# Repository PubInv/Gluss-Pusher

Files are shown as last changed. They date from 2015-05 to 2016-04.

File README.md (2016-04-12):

# Gluss Pusher

This is the working branch; if this is your first time here you probably want to go to our [public website](http://pubinv.github.io/Gluss-Pusher/) first.

This really needs to be changed to a new repository that talks about Gluss Robots rather than the Gluss Pusher per se.

### "The purpose of the Gluss Pusher is to enable new kinds of modular machines by making components cheap enough for hobbyist to build giant robots."

Please see [Sprint 3](https://github.com/PubInv/Gluss-Pusher/blob/master/Sprint3.md) for the latest progress.

Attempt to create simple, cheap linear actuator for giant robots and other tasks

This Repo is to hold research related to the invention of a new kind of linear actuator.

As part of the PIFAH project, this is completely open-source (both hardware and software) and everything be released either
under Creative Commons Share Alike, or the GPL.

As explained in the PIFAH/PIFAH repository, we welcome your contributions and participations.  Contact me to see how to
participate.

## Motivation

I would like to build robots based on large numbers of very simple components that can lengthen or shorten themselves.  Buckminster Fuller invented the Octet truss, a beautiful space-filling structure of alternating tetrahedra and octohedra. Or perhaps it would be more accurate to say that the universe invented and Bucky promoted it.

If we imagine a "truss" that acts like a "glass" we get a "gluss" that can move like a "slug".  That is, I want a system that can ooze about like a slug.

Linear actuators are standard components that can be purchased off-the-shelf.  However, they are rather expesnsive, at about $100 a piece. They are also more forceful and more precise that what we need to build an experimental "gluss".  Although it would be wonderful to spend $10K to build a power 100-element gluss, I think it makes more sense to attempt to use simpler components.

I also believe there is value in general for linear actuators in a cheaper, weaker part of the design spectrum.  Such actuators might be called "mechanisms" rather than "machines" in technical parlance. A machine deals with forces, a mechanism is concerned only with positioning.

# Related Links

http://en.wikipedia.org/wiki/Halbach_array

I don't understand why there isn't a good online simulator---perhaps I should write one.  This looks like it might work:

http://www.mare.ee/indrek/ephi/

http://en.wikipedia.org/wiki/Tubular_linear_motor

http://eprints.whiterose.ac.uk/852/1/wangjb15.pdf

I'm afraid I don't know enough about magnetism to really follow the equestions.  The purpose of this paper is to provide a model for linear permanent magnet machines.  I think it would be very valuable if you trying to optimize a design, or understand the force/current/voltage relationship. It is hard for me to understand exactly how to use this research.

This firm seems to make great ones, but doesn't list prices, so one can assume they are expensive:

http://www.linmot.com/fileadmin//user_upload/Downloads/databooks/0185-1100-E_1V0_Product_Overview.pdf

Here is a nice description:

http://machinedesign.com/news/linear-actuators-get-servo-look

So the terms "linear motor", "direct drive actuator", "tubular permantne magnet motor" are all used in this area.  The central rod should probably be called the "thrust rod".

This PhD Thesis looks excellent by Bryan P. Ruddy looks excellent:

http://hdl.handle.net/1721.1/78177

Reading Ruddy's dissertaton, it seems like the real contribution that I can make here is to move this out of the laboratory and into the realm of practice.  If we can make this kind of work available to hobbyist and the maker moverment, it seems that we could make very rapid progress on a really fundamental technology.

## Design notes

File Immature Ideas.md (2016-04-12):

# Idea: Use a Ferrofluid to create a simple actuator

I recenctly purchased and played around a bit with a ferrofluid. Because it is attracted to a magnetism, it seems
likely that if we put ferrofluid in a cylindrical bladder, we could apply a field to draw the fluid into a lump
(perhaps in the middle) thereby shortenining the cylinder.

# Idea: Can we use a simple air-gap filling apporach

I now wonder if we could modify the geometry of a solenoid to make a "long-throw" solenoid.  I believe the
basic prinicple that iron will be pulled in to fill an magnetized air gap could be used.

In this approach, we produce relative long magnets and use a relatively long iron core.  I don't know 
how much force is exerted in this "long model", but if enough is exerted, this could be a very elegant solution.
I think I can test this very quickly with the equipment that I have, though it will be hard to 
quantify---I need to get scientific and skilled at quanitfying these forces.

* * *

After a simple test, this seems not to be very useful.  the force for a piece of iron to be equalized between the two poles of a magnet seems either nonexistent or so low as to not be useful.  I suppose that my intuition was simply wrong about this.

# Idea: Using symmetric coils as both sensing and forced drivers.

It seems to me that if I have a set of symmetric coils arranged on the magnetic comb at something other than the comb periodicity, it should be able to detect where we are without additional sensors by applying slight currents to one comb while listening to voltage change in the other combs.  It would be very elegant in this way if we could determine our physical state.  This is simpler if you imagine a toroidal comb, rather than a linear comb, but the point is perhaps the same.

If you know where you are, you know which coil(s) to drive and which direction to drive them.  As an experiment, we could see if we can listen with an Arduino for slight motion --- even sonic frequency vibrations!

This is very elegant, because you are using more "smarts" --- putting more intelligence into the microcrontroller, without the need for hall-effect sensors (which could be used as well.)

The whole system is also thus becoming more "alive" --- it could tell when it is pushed.  It could even be pushed again something and perhaps determine how yielding it is. It is also inexpensive. Such a system could avoid the need for locking with a solenoid, by replacing it with active locking and active resistance.  This could be an extraordinarily elegant system.

# Idea: Universal rotation system

It would be really lovely if we got the above system working and then builded a true 3-degree of rotational freedom joint using the principle of geodesic dome construction to produce radail "combs" that could interact in the same way.  Imagine an omni-triangulated robot that had true 3-DOF manipulators!  All basically built with nothing but magnets and coils.  The geometric design freedom would be tremendous.

# Idea: (For Demonstration) An winged man costume...

This is sort of a cosplay idea.  Build a chest harness that has a back or chest keel.  Attach wings.  Have the linear actuator drive the wings based on buttons actuated by the hands (or in a harness.)

# Idea: Using Ferrofluid in a tube to extend the reach of the linear motor...

A fundamental problem with my current desigs is that you can only have so many magnets in contact with some many coils.  The higher the number in proximity, the more efficiency you have, but the lower stroke length.  The higher the stroke length, the more magnets or coils are wasted.  This could be changed by some complicated repositioning, but it would seem only at the expense of great complication to the moving parts.

However, what if ferrofluid confined to a tube would allow us to to make a magent of essentially changing length?  Then we could magnetize the thing with a single coil in a static position, but move the end (and the point of greatest flux change) to any position within the tube.

# Idea: use the comb and rotational magnets to produce latches....

Probably these need to latch in both directions to get the wedge effect, but that should be entirely possible.  I believe that by placing extra magnets in the carrier (not the push rod) and simply having them rotate out of the way in the presence of an applied B-field (which is easy to achieve), we should be able to make a physically strong latching system, at the cost of some increased weight in the carrier.  This would make a capactitor based "pump-and-rest" system more reasonable, and avoid us enterring a heavy duty cycle.

# Idea: using a twisting motion of the pushrod to lock it in place.

The Gluss Pusher currently doesn't have a way to lock the pushrod in place.  One way would be to have tabs added to the push rod, and grooves in the channel with slots.  By rotating the pushrod, you would free it for vertical motion, and by rotating it back you would lock it in place.  The rotation could be done with magnets in the push rod, or even rollers.  I think this would make it a lot less elegant however.

## Idea: Robotic Massage

One of the things that could be done with a 3-Gluss-member system is to make a massage robot.  The idea would be perhaps to put a ball or wheel at the end to a tetrahedron and have it pummel and roll the client. No doubt it would require a bit more sensing to be comfortable and a control mechanism, but in principle it should be possible with my system at low cost.

## Idea: Fire-Hose Robot

A Gluss could potentially climb into the window of a burning building, carrrying a fire hose.  (This idea came from a conversation with Jacqueline Kazil.) This could be controlled by a firefighter on the ground controlling a model. This would potentially allow water or a flame-retardant to be delivered more precisely to the source of fire.

## Idea: Tent Setup

This idea also came from a conversation with Jackie Kazil.  Imagine a gluss used to automatically setup a tent frame very quickly.

## Idea: (Important)

I believe we could construct an augmented octahedron. That is, make an octahedron, and add 4 tetahedron that will act as legs or pseudopods. The point that aims upward can shift to shift weight so that one of the legs may be lifted. I suspect in this way we could build an effective, and relatively inexpensive, walking robot, that would remain would have the advantages of gluss.  That is, it would be capable of other configurations as well, while remaining completely polymorphic.  Note: Possibly this would require a different a rotor, which would not be too hard---not sure about that, I have to check the math. 

This would require 1 octahedron (12 glussions), plus 4 legs, each requires 3 additional glussions --- so a total of 24 glussions.  At current prices this would cost one about $2400, which seems rather expensive.

Note that this geometry the center point would touch the ground in the most relaxed position --- although if they maintained some eccentricity, this might not be a problem, it is possible that better designs exist. For example, we could easily adjust the platform---but then we would be deviated from our basic principle of using only standard glussions.  Perhaps it is best just to use standard glussions and accept the eccentricity.  I don't particularly relish spending $2500 to test this idea --- but note that the resulting robot would be much larger and possibly capable of carrying much more than most robots.

## Idea: Maybe we can make really cheap by making a linear induction motor....

Last night I did the math and it requires 13 octet pairs to build a mast capable of forming a circle with a Q of 1.5. That works out to 108 glussions. At $70 a piece, that's a lot of change. My permanent magnet based system can potentionally lower that price, but only so much.  If we could use a linear induction motor instead, we could start to get really cheap---possibly $15 per glussion.  Of course, the controller will still be needed, and such a system won't hold its position without additional hardware or constant power---but still, a 5-fold cost reduction is worth exploring.  After all, the screw-type actuators also collapse under a sufficently high backdrive force (31 Newtons, in the case of the Firgelli model I am using.)

<br /><span xmlns:dct="http://purl.org/dc/terms/" href="http://purl.org/dc/dcmitype/Text" property="dct:title" rel="dct:type">PIFAH: Immature Ideas</span> by <a xmlns:cc="http://creativecommons.org/ns#" href="https://github.com/PubInv/PIFAH" property="cc:attributionName" rel="cc:attributionURL">Robert L. Read</a> is licensed under a <a rel="license" href="http://creativecommons.org/licenses/by-sa/4.0/">Creative Commons Attribution-ShareAlike 4.0 International License</a>.<br />Based on a work at <a xmlns:dct="http://purl.org/dc/terms/" href="https://github.com/PubInv/PIFAH" rel="dct:source">https://github.com/PubInv/PIFAH</a>.

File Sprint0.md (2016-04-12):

Note: This was actually Sprint4 or PIFAH, before I decided to make this its own project.

## Stories

* Figure out if I can get the 1/4" x 1/2" magnets into a tube for making the actuator.
* Experiment with apply the current loop to these magnets---I believe we will get a strong push from them.
* Try to construct an initial prototype of the actuator using just a power supply.
* Construct a new MOSFET circuit (similar to old one) and see if I can drive it fro the Arduino to properly
move the actuator to a different state.
* See if I can order an H-Bridge that will allow me to reverse current flow in a way that will allow us to change
the actuator state in both directions.

As a matter of procedure, if I can get anything working I will create a new Repo for this project.

## Log

In the last two days, since Mini Make Faire, I worked on the actuator.

I build a coil and a set of magnets, placed in some foamcore.  I was able to get it to move.

I think worked much harder, and built a good plywood holder for 6 of the 1/4 x 1/2 magnets. I held these in place in polycarbonate taped together.

I tried it, and it didn't work.  That is, it twitched. It did not do what I need it to do: move to one of the "pole" positions based on the current.

I was quite surprised that the force was insufficient, although my coil has only 30 or 40 turns, and mow power supply cuts off at 5 amps. Nonetheless, it was a failure.

I am attempting to construct the magnetic actuator anew with a poster-board wrapper. Hopefully this will be both "slicker", having less friction, and will be lighter. It is possible this model will work.  It is possible that I will have to go back to the drawing boards.

imag0170

imag0161
imag0163
imag0165
imag0167
imag0169

## Wednesday

I learned that the tightness of the windings really matters.  I'm now getting a few ounces of force, I imagine.  I have a strange assymetry in the actuator I built that I can't explain.

I tried using an aluminum tube and it seemed very weak --- possibly the Krebbs effect at work.

I embedded two magnets in a wooden dowel.  When that is placed inside a PVC pipe with a coil around it, I am starting to see the kind of behavior I expect, though the weird assymetry persists.

I am very tempted to buy some better materials---I know that will make a difference, but it is also a delay and an expense.  I want to carry on with as many experiments as I can at present.

General lesson:  It is really hard to get a coil 3/4" wide to discrimnate a magnet only a 1/2" long.

I've got a bistable system, but it should have 3 or 4 poles (for 2 or 3 magnets), that is, 3 stable conditions.  In stead it seems to "wash out" in the middle.  it is as if the flux within the coil is swamped by the flux at either end.

## Wednesday Night

I am a fool, but I have done it! My expectations were wrong.  It is clear if now that if you build a "comb" with alternative North and South poles each one will represent a stable position (probably just on the opposite side of the charged coil.)  I can now, just by switching power, move randomly through 4 stable states with 5 magnets.
The motion is random now because I can't control which state it will move to when I switch current direction driving it out of the current state.  However, that can be fixed easily in the future.

I think this is a great success.  IF this can be tied into a frame that provides permanent magnet latching, and IF I can get an Arduino to successfully switch on and reverse power (such as with the MOSFET circuit I built earlier, then it seems that I might have actually created something useful: A cheap, long-through, multi-polar linear actuator.

Note: I messed up the spacing on the magnets in my actuator.  I may have to redo in order to get the latching to work properly. Ideally I would have better materials by that time.

## Friday Night

The two-dimensional attempt basically didn't move very well.

I switched back to a tubular approach, basically re-inventing the tubular linear motor.

This actually "worked" in that I could easily drive a 2" crest-to-crest change using the coil.  This is similar to a 
coil gun, with a permanent magnet in place.

imag0171

imag0172

imag0173

I have learned a lot this sprint, though perhaps that is only a sign of how ignorant I am.

Let me try to summarize:

* Magnetic field computations are actually quite difficult. Unlike electrostatic compuations, the "field" the field is modified by anything ferrous. It is in fact quite difficult to to analytically figure out the forces. Also, there is no good free online simulation!
* I believe it IS possible to build a repulsive system, but it is rather complicated. Naive approaches produce a "pinching" of attractive approaches.
* The tightness of the coil is really quite important.  A lot of flux is wasted if the coil is larger than necessary.
* My system provides no control --- I can change state but can't control direction. It is fairly obvious how to control it with a separate additional coils.
* The best way to really handle this is to have a microcontroller really understand the position of the shuttle. I don't know a good way to do this.
* This is obvious, but if you take iron it will move to a central position on the coil.
* Using my 8-volt system with a limited amperage, I can make a nail repulse a small magnet.  However, my home-made electronmagnes are in general not as powerful as the neodymium magnets.
* I CAN easily build a latching system with the permanent magnets.  It is interesting to imagine a latching system that cooperates with the electromagnetic motion.  However, I now believe this is a distraction---getting the driving working is hard enough, and we can latch with a solenoid mechanically to be stronger and cheaper (I think) than we can ever hope to be with this pure magnets.

I have created a new repo: https://github.com/PubInv/Linear-Actuator and will probably move much of this file to that repo.

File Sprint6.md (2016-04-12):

Sprint 5 saw the successful completions of the [CoilChoice tool](http://pubinv.github.io/CoilChoice/).
It was a strenuous effort and I am quite proud of it, though as far as I can tell nobody has noticed it yet.

# Theme

I believe the main theme of this sprint is to return to more 3D design.

I have what I believe is an idea for limited ball-and-socket joints for the Octet joints that is worthy of the title
"invention".  It is worth about 1 micro-Fuller, I think.  

In addition to that, I need to redesign the stator, and produce a stator-tube end cap to hold the position sensing electronis.
Basically we are now moving toward a completely scalable and independent "Glussion".

### Measurement of force of existing system.

At 12 volts, turning scale sideways, the highest force I can measure in a holding pattern 98 grams. 
At 18 volts, it is 160 grams. At 24V, 235 grams. At 30 Volts it began smoking very quickly! This heat definitely softened, perhaps destructively, the PLA plastic.

I expected this to be low, but this is really bad---I estimate we need about 10 times this much force to have a viable system.

I believe I am using 32 gauge wire right now. CoilChoice suggests that I should use 30 gauge wire.  However, it still seems somewhat unlike that we can get up to a 22 newton (1 kilogram of force system) with a 2-amp limitation.  It seems absolutely essential that we go up to 5 amps.

Our current coils provably have about 250 ampere turns at 12 volts. A 5 amp system using 28 gauge wire should provide about 750 ampere turns -- about 3 newtons, which still sucks.  

It seems possible that I should perhaps abandon this approach, or at least get the Phidget's actuators for comparison.

Quite possibly this whole project is bogus because of the difficulty of producing force in this way.

I think is pretty important now that I test the lithium io battery approach.

Using this battery:

https://www.fasttech.com/product/1895004-dc-1298a-12-6v-9800mah-rechargeable-li-ion

I was able to get 148 grams of holding power.

# Formulation of a multi-glussion connector problem

Assuming that we use a symmertic circular section of a sphere as the center of our disc, what is the greatest possible ration of L to S, where L is the longest distance and S is the shortest of our glussion, that you can connect with a tetrahedronal (or planar) connector?

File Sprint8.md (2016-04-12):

# Sprint 8 - Saturday October 3rd

Very thrilled with with publication of the [Turret Joint](https://github.com/PubInv/turret-joint). Initial test are 
promising, although far more testing is needed.

We now have an actual robot, the "GlussBot #1"!

## Basic Goals for this Sprint

* Publish photos of the GlussBot #1 -- done
* Clean up existing Arduino code and publish both the way to hook up the motor controller and the code
* Write a true Cartesian space controller
* Produce a test routine that moves GlussBot #1 through its full range of motion. -- done
* Publish video of moving GlussBot #1 and explain what it is doing -- done
* Prepare for the October 17th open house at TechShop --- try to get a fun demo for kids! Possibly show marking or 
etching inside a bowl or other structure.

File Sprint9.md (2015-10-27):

# Status

Progress was interrupted by my trip to Maker Faire Rome on behalf of Engineers Without Borders.

Nonetheless, great progess has been made.  I now have a complete octahedron-tetrahedron cell made out of
carbon fiber tubes (with my three actuators.) Mechanically we now have but to purchase and actuators and replace the
rods with the actuators.  The Turret Joint has been further refined, developed, and tested, though more work needs to 
be done.

However, we can now shift our focus to the construction of a proper enclosure for the electronics and batteries
so that we truly have independent and repeatable cells.  We now have three physical cells, and one with electronics.

Most importantly, Marcus Lopez is interested in helping, particularly around the construction of the enclosure. This is
really the first person who has seriously offered to help.  This is far more important than any electromechanical 
progress, because the purpose of Public Invention is to form a team of inventors helping all humanity.

# Stories

* Repair the immediate breakage I made last night during destructive testing
* Test and publish photos and videos of the existing system
* Choose and purchase a battery
* Give Marcus everything needed for enclosure design (including sample materials)
* Review the mathematics of my post-width calculation---I think I have that wrong. Testing should reveal it.
* Select hardware for and experiment with radio control.
* Publish the idea of the cuboctahedronal walker.
* Purchase a large complement of acuators.

# Major Goals

* Build and demonstrate a quadrupedal walker made out of gluss by the first day of 2016.
* Demonstrate a smart-phone based control system.
* Design a low-cost robot that anyone can build at home to creatively apply gluss technology to new problems.

# Motivation

Let's review why we are doing this.

Current robots are not versatile. They neither mimic nature well nor enable creativity.

Gluss will enable people to do things they can only do with very specialized machines today. Such as span a river, climb high into a tree, prop up a dangeours building, move heavy objects in awkward situations, lift structural elements into place, dig people out from collapsed buildings, pretend to be Doc Oc, build huge temporary structures, build walking tents, build moving shelters, build expandable shelters, lift shipwrecks, and explore caves.

But you can probably think of more than that---my imagination is a bit limited.

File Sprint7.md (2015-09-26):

# Sprint 7

I spent most of the end of Sprint 6 (and all weekend) constructing a new kind of joint---a "turret" joint, which I will
document as soon as testing allows.

## Notes on Firgelli Linear Actuator

I also purchased 2 Firgelli mini linear actuators.  The are expensive -- $80, but my initial results suggest that they are excellent.  They are very strong.  The model I have is the L16-140-35-12-P. It really does seem to produce 50 Newtons of peak force at 12 Volts drawing half an amp.  It has a built in potentiometer that gives you an absolute position.  I actually don't trust the potentiometer system---I suspect it is mechanically unreliable compared to the light-based sensor.

Nonetheless this is a real challenge to the create of the Gluss Pusher as a separate tubular linear motion.  Although my approach may be cheaper, and have a faster throw, it is hared to imagine producing 50 Netwons of force with my existing system.

Obviously, the Gluss idea could use either system.  However, I now think I will try to mount my joints to the Firgelli actuators to test those joints.  This should at least make for a nice demo, and give us a way to make a scalable system.  I'm hesistant to believe that at a $70 price point this will really be acceptable for a 20 or 50 glussion gluss, but I'm willing to try it.

## Goal for this sprint: Document the Turret Joint

The goal for this sprint is to document the Turret joint, possibly using the Firgelli acuators as an example.  I am writing 
this on Tuesday, and am attempting to 3D print some of the last pieces I need to form a tetrahedron as I write.

I will now attempt to design a mounting system to use the Firgelli actuators.

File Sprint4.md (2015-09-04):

# Sprint 4

## Theme

Trying to get motion reliable with new stators.

## Stories

* Clean and wind the newly 3D-printed stators and see if motion is reliable.
* Use larger potentiomter somehow to make an easier to control system.
* Test the position sensing with the newly created white pushord caps
* Order some bigger (and more) carbon fiber tubes from RC foam.
* If successful, make a new video documentin everything
* If successful, publish new designs at Thingiverse

## log

Tuesday, 2:37 pm

I have wound the new stators.  They work fine.  Positiong sensing also works great!

However, I have two very annoying problems that are stymiing further process:

My Arduino (or relay shield) seems to lock up.  Often the Arduino is still listening to the serial bus but a relay is stuck in the "on" position, which means that we are heating up one of the coils.  Possibly this melted my stator a little, which is why I now have mechanical problems.

After going for a run, I am now convinced that I need to redesign the Stator YET AGAIN. I don't know what that means...I am in favor of iterative development, but perhaps more Big Design Up Front would have been better.

Basically, I think it is time:

* To put the two coils closer together, in order to minimize the distance that we have to touch the push rod.
* Remove the colimating part of the stator for the pushrod, so that as much as possilbe the pushrod is supported by the rear end cap and a single point (unfortunately about an 1.5 inches long) at the coils.
* Make the Stator reach back as far as possible to have a ring to hold the stator tube in position.  This should be done with a truss-like structure to make it stiff and still get a reasonable print time.

I am close with the calibration code, I hate to take the time to redesign and re-print the stator. However, I don't have any good way of disassembling the current pusher to solve the stickiness problem.

I could try going up to 24V in the short term, I suppose.

I guess I really need to make a short video of this.

The mechanical "stickiness" of the system is very annoying.  It seems to have developed after I epoxyed the Stator tube in place.  This makes it significantly hard to test everything.  If I increase the voltage I can get past the sticking points, but that is a terrible way to deal with this problem.  Unfortunately I have to figure out a better way to make a bearing.  I think linear bearing would be great, but they are normally made of steel, which interacts very badly with my magnet-filled pushrod.

I want a simple solution that will let me test this, rather than having to "invent" a solution.

Possibly I need to start using bearing like these on the ends: http://www.igus.com/iPro/iPro_02_1008_0000_USen.htm?c=US&l=en

But that will not solve the problem of my pushod not going through the hole, which must be tight.

### Wednesday Morning

Yesterday I took the laser cutter class at tech shop.  I am tempted to redesign the stator yet again.  However, I think it is more important that I make a video showing my current work, by work or by crook, first.

The redesign needs to focus on several points:

* I don't want to have to epoxy things, as this makes it impossible to disassemble.
* I want to start designing a way to put the Arduino, and possibly the breadboard, onto the system.
* I need to design the end cap to held the electronics in a reasonable way.

### Wednesday Afternoon, 1:00 pm

Okay, video made. 

I think before I do the redesign, I really need to use the new positioning system to prove its value.  There are several approaches (or at least experiments):

* Experiment: Kick a coil and simply start reading the voltage value, and see what happens if we turn the coil off right when we reach the correct position.  I expect it will overshoot significantly.
* Experiment: Write a function that reads the position, and turns on "Hold Position" as we deviate from that position.
* Experiment: Change the "P" function (absolute positioning) to read the arbitraty position and try to move to that position, whatever happens!

## Wednesday Afternoon, about tea-time.

Great progress.  I fixed a stupid software bug that was adding confusion.  I am now reliably (unless I get stuck!) moving to various positions. I have written a "smart hold" function---that is, the system will monitor its position, and if you pull the pushrod out of position correctly attempts to restore it!  That is a very enabling feature, partially making up for the fact that we don't have a physcial locking mode.

It is now the case that is is a COMBINED position sensor and linear actuator.

Still plagued by stickiness in fully retracted and extended positions.  Also, I am generally operating at 18V, which is very unfortunate.

I now believe there are three tasks to be done:

* I want to make the motion between multiple stops smooth.  That is, now that we know (approximately) when we can cross a threshold, there is no reason to move in short stops. So we should be be able to have fast, smooth motion. In a deluxe mode, we would actually model the velocity of the pushrod and build a model of forces for acceleration and deceleration!
* We need a systematic study of the best way to generate the MMF. I know a lot about coils but there remain some questions, some of which need to be verified experimentally.  At present, the system is of marginal usefulness. I'm estimating it exerts about 12 ounces of force.  If we can get that up to 5 pounds we will have a much more reasonable system. Of course, that is possible with more coils and more power (or even more magents) but those increase our costs.
* I do believe we need a better physical design.  I don't want a system that relies on epoxying the stator tube in place, as I do now.

### Thursday morning

I got the "hold position" function working.  This is actually TREMENDOUS progress.  Unfortunately I seem to be sick. But nonetheless yesterday, although exhausting, I got an enormous amount of stuff done.

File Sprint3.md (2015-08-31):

Monday, August 24, 2015

# Sprint 3

## Status

I have not been maintaining my process discipline very well.  A lot has happened since my Sprint 2.

* I did construct a controllable Gluss Pusher.  You can see it in the video that I posted.
* At considerable effort, I made a 10-minute introductory [video](https://youtu.be/cpzPVwBoE_4) to the project.
* I have created an attractive 3D-printed stator. After much trial and error I am very happy with this. The new stator
and the new carbon-fiber pushrod work very effectively.  I will post a video of this very soon.

## Goals

* Document my 3D-printable design to the level of easy reproducibility
* Move closer to being able to create a 2D Planer Robot with two Gluss Pushers

## Stories

* Publish Fusion 360 designs - done
* Publish STL file at Thing-i-verse - done
* Measure voltages produced by motion against coil in order to see if we can build closed-loop detection of our position.
* Switch to using the motor controller to see if we can get micro-step control.
* Cut Acrylic tube in order to have actuator stability.
* Consider a "shaking" of one coil to see if we can detect other coils.
* Consider possibility of building coil rings into the stator further down in order to provide true positional control.
* Compare possiblity of using coil ring with Hall Effect sensors.

## Log

Experiment #1: Does moving the pushrod by hand produce a measure voltage?

Monday 12:04 : it is seems very clear that we should be able to use the non-active coil to verify each move. In my new stator design, simple movement by hand is easily generating 2V! (Actually, we are probably pay that cost---if we could pump that back into our system, we would be more efficient---but that is a level of control beyond the immdediate need! 

Experiment #2: If we program the Arduino to "Shake" the pushrod without making a move, can we see see the result in the other coil in a way that lets us tell where we are?

Yes, afer doing millisecond sampling it is very clear that we can read the motion of the coil.

DANGER: A sharp motion could produce an overvoltage (more than 5V) and fry the Arduino.
PROBLEM: I need some sort of circuit for sensing negative voltage as well.

However, given the fact that I can apparently sample very quickly and compute all of this, I think we should be able to write a robust "did I move" function or even "apply energy until I move."

Note that we need to protect the system from overvoltage and read negative voltage.  This looks particularly valuable:

http://www.symres.com/files/scalebias.pdf

Tuesday 11:34

Last night I tried to get build a voltage divider to sample the voltage in the non-active coil and it failed miserably and mysteriously.  I suspect that I had something miswired.

I am not sure that reading the inactive coil is in fact the best way to do positioning.  It will never allow you to sense absolute position, for example.  However, I want to debug this to understand what I did wrong.  I supsect that some sort of LED-based direct sensing of rod position will be far better.

It is exciting that we are now addressing the question of reliable motion rather than simply motion itself.

Wednesday Night

Curse me for a fool.  I now know that I designed the coils too far apart in the 3D model, which is why it is uneven, and might cause all manner of other problems.  Also due to weird constraints I have to completely redo it.  I will do that tomorrow to be ready for the Saturday morning trip to Techshop.

However, more importantly is to work on the photo-cell detection idea.  That is what I will work on tomorrow.

Thursday

I've been experimenting with a closed loop solution.  Basically I plan to shine an LED into the stator tube and detect the light level.  My initial experiments suggest that  this will work. I would rather use a white-light LED. However, using a green LED, I can measure resistance values on the scale of 100K ohms, varying pretty smoothly as I move the pushod.  So today I am going to set up an experiment to attempt to do this.

Following my ARDX, I am going to make a voltage divider and try to read this with an Arduino.

3:00 pm

I believe I have had a great success.  I bought a 5mm 7000mcd brightness white LED from RadioShack.  Placing this at 5V from the Arduino with a 546 Ohm resistor. I soldered this onto a wire.  I took a standard photocell (the one that comes with the ARDX, and, as the ARDX suggests, placed it as the lower resistor in a voltage divider.  The 5V from the Arduino is applied to the voltage divider, that then Vout read with a multimeter.  It then very clearly varies between about 2.8 and about 4.5 V as the pushrod is inserted and withdrawn from the tube.

Although I have not yet digitized it with the Arduino, this strongly suggests that at low price ($2 at most) we can read the position of the pushrod.

This technique is probably unreliable in the sense that it requies calibration.  However, are strategy is to use "smarts" in the form of the microcontoller and to avoid extra components in the BOM.  And, our system is already a stepper motor---it should be very easy to auto-calibrate it!  (This will be a teensy programming challenge.)

I wonder if this worth making a video about?

(Actually I just discovered the $20 [motorized potentiometer](https://www.sparkfun.com/products/10976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) at Sparkfun which potentially makes this whole project obsolete. I will have to order some of these to test with. Sigh.)

Maybe I should document the light-based linear position system completely separately.

## End of Sprint

Finally, I have reprinted my parts after fixing the fact that the intercoil distance was wrong.  Hopefully this will solve the reliability problem I have been having.

In Sprint 4 (starting tomorrow morning), I will wind the new stator and test it, along with the 3D printed white end cap for sensing.  If it moves reliably, then unquestionably Sprint 4 will be primarily about using the sensor to make motion fast, smooth and reliable --- it will be primarily a software sprint.

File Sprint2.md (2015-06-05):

# Goal: A working controllable acutator

My general hypothesis is that with a non-polarized core I should be able to make an Arduino controllable actuator.
It is not entirely obvious that I can do this without some control circuitry to determin position, but presumably if
I substitute human control for this, I can make it work.

For example, at the end of this sprint I would like a system consisting of:
* An Actuator,
* An External Power source,
* An Arduino, and
* a couple of buttons,
which allows the actuator to move in two directions based on pushing the buttons.

June 1st,2015

I have now played with the Seeedstudio v2 Motor shield.  The fact that it is limited to 2 amps seems a hindrance, 
although the fact that it allows polar control of two motors seems pretty useful.

However, I am going back to using my 1/2" Neodymium magnets and my large tube, at least until the acrylic gets in.

Using the arduino, I can now pop the carrier back and forth, though with only one coil I can't control it.  The 2 amp limit is no problem with the bigger magnets.  Occasionally the carrier gets stuck in one place, and slight touch moves it.  I hope to improve that.  Unfortunately, I have to take my machine apart in order to do that.

June 2nd, 2015

I now tried using the second "kicker" coil.  It DOES indeed seem to allow me to control the direction of motion.  Using this coil turned on for 100 ms before and after firing the main coil, I can make it go completely to the left or completely to he right (by switching the terminals on the second coil.)  It is not 100% reliable, but it does work. 

I am now tempted to make the acrylic piston, in order to avoid the slight friction inherent in my taped-up magnet carrier.

NOTE: By reducing the duty cycle on the second coil (to 20% in the case above), I greatly abate the problem of overheating of that coil (I used very thin wire on that coil.)

NOTE: I would now like to use a button press to initiate left and right action. I bought a kit that has two buttons (tiny, and weird), which I have not used.  I will have to put them on a breadboard, but let me use that.

Evening:

I constructed a 10-magnet piston out of acrylic tube.  Unfortunately, it has too much weight and friction, it doesn't slide easily.  I need to both lubricate it better and move to an Acrylic Tube (just a little thinner) and possibly try to improve my coils.  If I could double the number of turns on my coil (which is not trivial), that could really make a big difference.

June 3rd, 2015

Some learnings:

I tried using baby oil as a lubricant for Acrylic-on-PVC.  As far as I can tell, it deosn't help much.  Nor does it make Acrylic-on-Acrylic better. Basically, I need to go to a bearing system of some kind.  This is a huge mechanical complication, though I suppose that I can must do it.

BTW, you can really feel a big difference at 5 amps vs 2 amps.  I suspect 5 amps would overcome a lot of the problems I am having --- but the Motor shield doesn't support that.  So basically I have to either make my own circuit (which is entirely possible, but a cost in time), or possibly by simplying winding a better coil (and taking advantage of a slightly different smaller diameter for my outside pipe to get more windings on there.

Note that at 5 amps my coil gets hot quickly.  The whole idea of this system is to have a low-duty-cycle system, which IS possible with Arduino control, but is hard to do with just my power supply by hand.

Observation: My think (30 AWG) magnet wire gets RIDICULOUSLY hot at 5 amps in about 1/2 of a second.  Obviously that will have to be used with a very low duty cycle in that case.

And BTW, Acrylic is not a good plastic to use for this kind of work.  It is terribly soft and not very slick.  It looks nice, though.

Idea: Right now I am wrapping the coil around the outside of the pipe.  This is confusing the electrical and mechanical system.  I could cut the outer pipe --- that is, essentially using two structural pipes on the outside, I could decrease the area of the coil by the diamter of the outer pipe --- that is, using only the thinnest membrane to protect the pipe.

So now we must ask ourselves: what is the greatest learning capability for the least effort?  Although I clearly need to quit using the motor shield and design my own circuit that allows more power to be dumped quickly into the coil, that will take some time.

So I am tempted to rewind my coils at present, and see if I can get significant motion that way.

I rewound the coil, and it is much more powerful in the tighter configuration.  I am pretty happy about that.  Unfornuately, my lack of bearings is really creating a problem.  I really need to create a better bearing in some way even to test this.  Obviously you can buy them, although they are a little hard to find at low cost.

Also, I don't be believe my program is quite operating correctly at the moment.

* * *

Resolved:

I think I need to do several things:

* A really need to create roller bearings.  I believe I can do this out of finishing tails or other nails placed in proper holes, or by using aluminium rods (or even plastic rods.)
* I MUST find a better way to make coils.  If necessary, I must manufacture the frames myself.  A proper frame HAS to have rails to keep the edges contained and MUST be stiff enough to not change diameter when wrapped tightly.
* I can put an aluminum tube in my acrylic tube to hold my magnets precisely.  If precise enough, we should be able to use multiple coils, which in practice may be a big advantage.

* * *

June 4, 2015

FLASH -- I've been making a stupid mistake. By making my coils too wide in a clumsy attempt to pack more turns on, I have been spreading the North and South poles, thereby actually create a "dead point" -- a slightly stable point when the polarity is reversed.  Although I find making coils a tedious pain, I really need to create a narrower coil (I am using 1/2" magnets, a 3/8" long coil would be ideal) in order to see if that eliminates the dead point and allows me finer positioning control of the destabilizing coil!!!

Also, I need to get some nylon tubing --- the Acrylic is the least-slick plastic in the world.

TODO:
* Build a spool precisely 1/2" wide and try it with 30 gage wire.

I THINK the new spool is a success. It doesn't seem to have a deadpoint, but it is very hard for me to separate this issue from the bearing issue.

I now need to make another spool for the quarter-phase kicker, and then somehow build a better frame with a better bearing for the piston.

* * *

## Close of sprint

I think I am very close to a working, controllable system.  Unfortunately, I have to put this down for the weekend to prepare for and champion a team at the ATX Hack for Change Hackathon for Engineers Without Borders.

If I can pick this up on Monday, I want to:

* Create the quarter-period coil using a similar sturdy system to the main coil,
* Create some sort of home-made bearing better than what I have been using to decrease resistance.

When these things are done, I think I should be ready for a real test.  If that works, I will be ready to post a video and explore a huge number of possible improvements.

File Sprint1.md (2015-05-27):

# Sprint 1

There is a wonderful resource that shows that this is in fact rather complicated: http://coilgun.info/about/home.htm. 
I believe it would take me a week or two to fully understand the mathematics of that very valuable site. MIT has
made a contribution as well: http://ocw.mit.edu/courses/electrical-engineering-and-computer-science/6-007-electromagnetic-energy-from-motors-to-lasers-spring-2011/lecture-notes/MIT6_007S11_lec14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
which may be simpler.  I have not yet worked through the math.

Note that this is very colsely related to a coil gun, but of course there I am not interested in making a 

In fact magnetism in general is more difficult to compute than electrical effects.

In Sprint 0, I was able to move Neodymium magnets in a carrier effectively with homemade coils.  However, I could 
not control this.  I have since designed an approach with multiple coils that should allow control.  My goal this 
Sprint is to demonstrate this control ability, possibly beginning control via an Arduino.

### Self-doubt

It is very unclear to me that this is worthwhile.  I measure coolness in "Ellsworth" units, and benefit to the world in
"Bucky"s.  I believe this would be a 3 micro-Ellsworth project and 2-Bucky project if successful.  I think
it will take at least two weeks to demostrate this.  The chance of success is aobut 40%, so I the expected goodenss
is 1.2 micro-Ellsworths and 0.8 micro-Buckys. I am unsure that this is worth my time---that is why I would like
to have others comment on this.  However, I believe it is worth moving forward on.

## Stories

* As a skeptical investigator, I would like to prove that I can move the magnet using a multi-coil system. -- basically done now, with my shabby little three coils.
* As an investigator, I would like to prove that I can coordinate two 25-turn coils to move the 1/8" cylindrical magnets -- basically done, thought my equipment right now is terrible.
* As a robot builder, I would like to be able to control the motion of the piston with an Arduino, in whatever a
limited way that may be.
* As a hobbyist, I would like to know how to build an actuator (without consideration of force), for around $10 that
let's me move something with my Arduino.

## Equipment

I have a Seeedstudio Motor Shield V2. In principle, should should be able to drive two of my coils.  It's a little depressing that it takes that much extra hardware---since I am going to have at least 4 coils!  But I suppose I must try to understand this shield instead of trying to build my own MOSFET control board---something that I have been wanting to do for some time.

Unfortunately, all three of my current Adruino Unos are in use in other demo projects, and I would rather not cannbalize one.  However, I have an Esplora, and I suppose that if I use enough jumper cables I should be able to power it in that way.  I THINK I can use my power supply to provide up to 15V power to the Motor Shield and have it power the Esplora, perhaps --- not sure about that.

Once again, all of this is just showing how much I have to learn --- I barely understand how Arduino shields work.

BTW, I'm pretty sure that we can eventually build a simpler (less expensive) system for controlling the coils.

I need to get some thinner magnet wire, and possibly another Uno.

## Project for Tomorrow

So tomorrow I want to try to use my Motor Shield to control two of my coils independently.  I suppose that I should wire it through my Esplora.

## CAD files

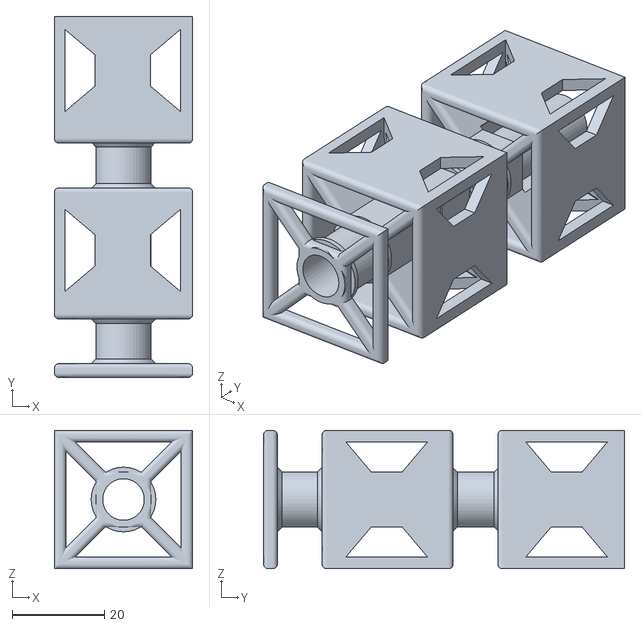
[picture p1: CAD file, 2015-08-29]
PhysicalModels/StatorV2.stl
30.0 x 78.3 x 30.0

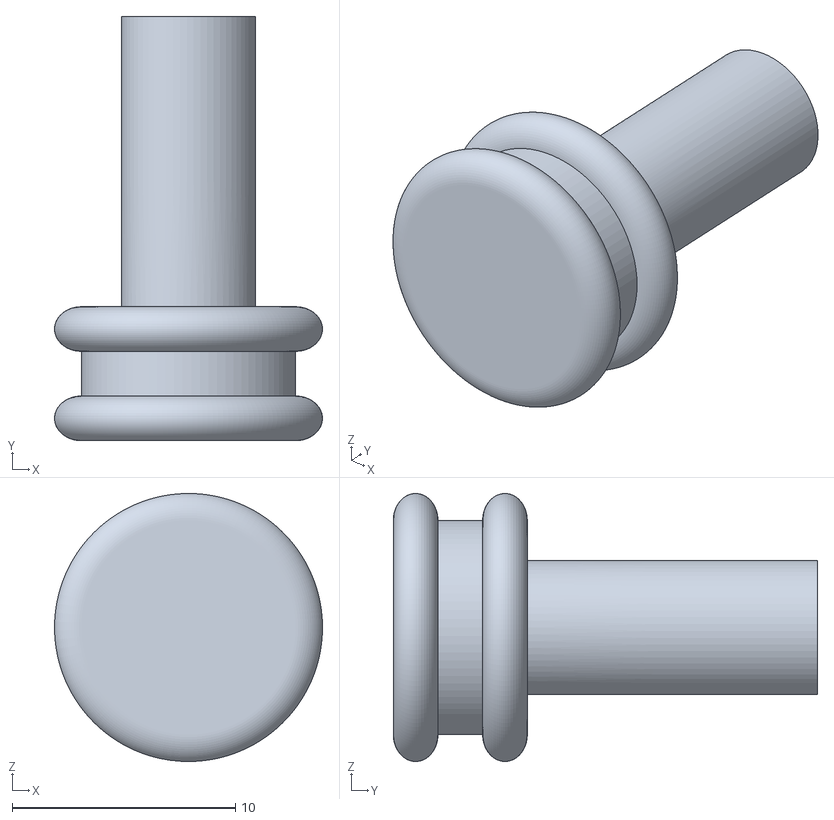
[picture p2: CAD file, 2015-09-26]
PhysicalModels/STLs/EndCapForStator12mm.stl
12.0 x 19.0 x 12.0

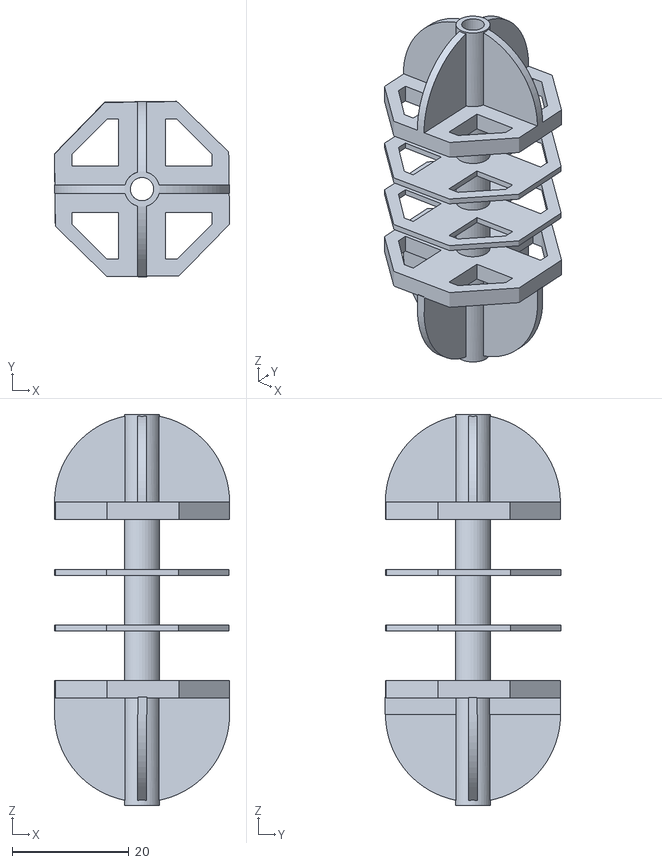
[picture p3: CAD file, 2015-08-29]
PhysicalModels/TinyStatorV3.stl
30.0 x 30.1 x 67.0

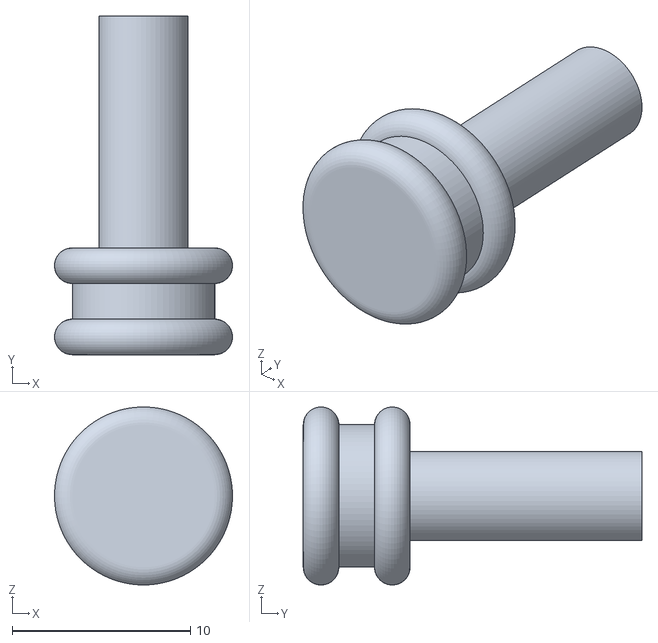
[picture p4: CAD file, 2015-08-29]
PhysicalModels/STLs/StatorEndCap.stl
9.99 x 19.0 x 9.99

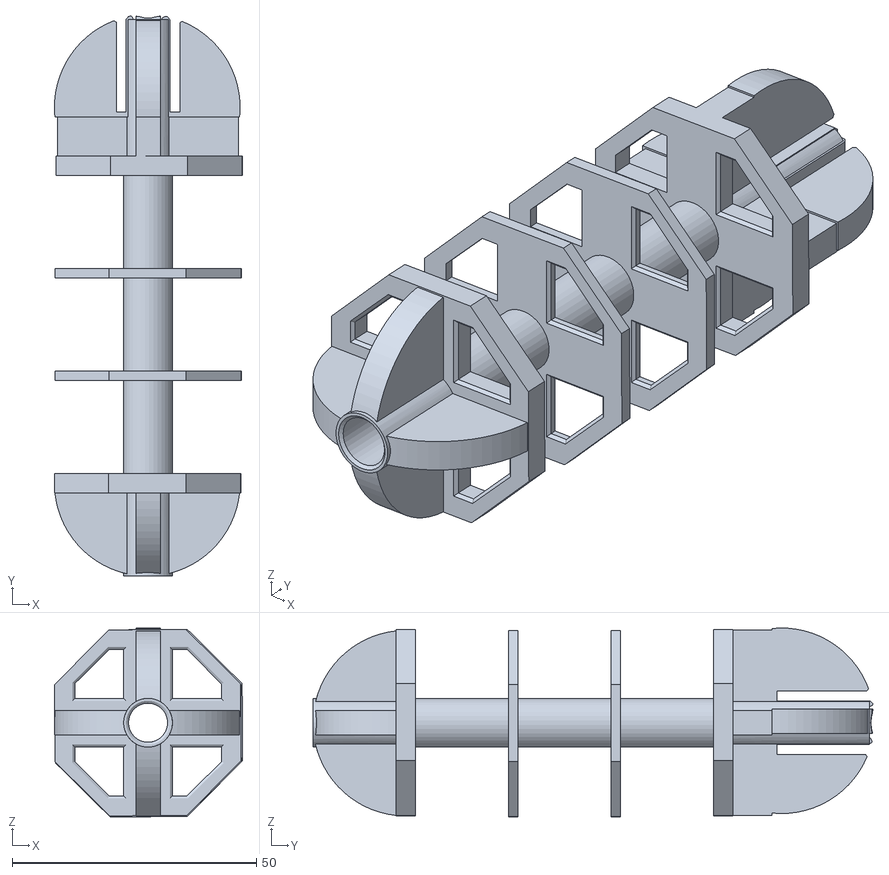
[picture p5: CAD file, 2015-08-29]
PhysicalModels/StatorForStandardSize.stl
38.6 x 114.7 x 38.7

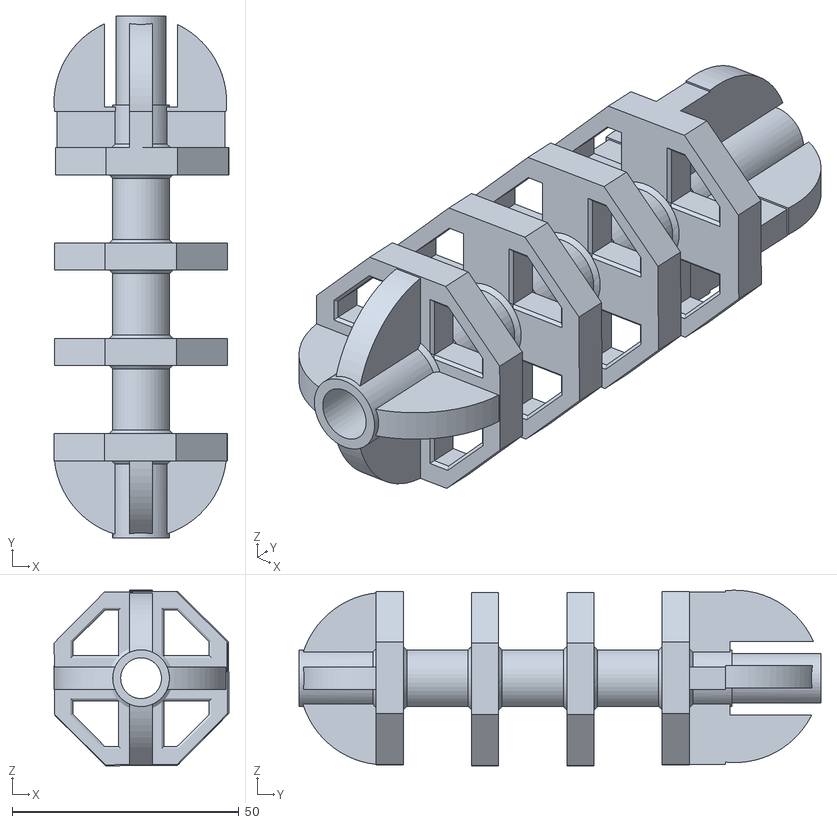
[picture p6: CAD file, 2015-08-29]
PhysicalModels/STLs/StatorForStandardV7.stl
38.6 x 115.0 x 38.7

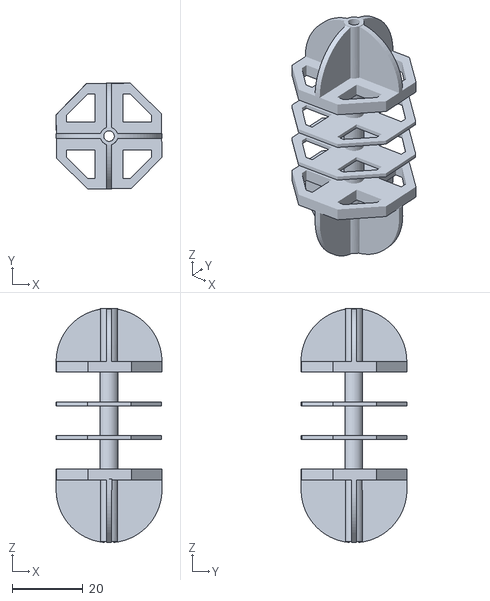
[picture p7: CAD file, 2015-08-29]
PhysicalModels/TinyStator.stl
30.0 x 30.1 x 66.3

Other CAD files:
PhysicalModels/STLs/StatorV2.1.stl

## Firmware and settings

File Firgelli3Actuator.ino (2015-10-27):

#include <stdlib.h>
#include <EEPROM.h>
#include <math.h>
#include <assert.h>

int ANALOG_PIN_P = 0;
int ANALOG_PIN_Q = 1;
int ANALOG_PIN_POT = 5;
const int ANALOG_VOLTAGE = 3;

int sign(int a) {
  return (a < 0) ? -1 : ((a == 0) ? 0 : 1); 
}


int pinI1=8;//define I1 interface

int pinI2=11;//define I2 interface 
int speedpinA=9;//enable motor A
int pinI3=12;//define I3 interface 
int pinI4=13;//define I4 interface 
int speedpinB=10;//enable motor B
int spead =127;//define the spead of motor
const int FULLSPEED = 255;

// Chosen to deal with duty cycle
const int CRUISE_SPEED = 255;
int pinI5 = 2;
int pinI6 = 4;
int speedpinC = 3;

// This doesn't make much sense with the FirgelliController
int NUM_POSITIONS = 14;
int Calibration[14];

typedef struct {
  int forwardPin;
  int reversePin;
  int speedPin;
  int potPin;
  
  int minV = -99;
  int maxV = -99;
} actuator;

// typedef struct actuator Actuator;

actuator act[3];

// At present I will pack the calibrations into EEPROM starting at this address
int start_address = 0;

void setup()
{
  
act[0].forwardPin = pinI2;
act[0].reversePin = pinI1;
act[0].speedPin = speedpinA;
act[0].potPin = A0;

act[1].forwardPin = pinI4;
act[1].reversePin = pinI3;
act[1].speedPin = speedpinB;
act[1].potPin = A1;

act[2].forwardPin = pinI6;
act[2].reversePin = pinI5;
act[2].speedPin = speedpinC;
act[2].potPin = A2;


  pinMode(A0, INPUT);
  pinMode(A1, INPUT);
  pinMode(A2, INPUT);
  
  pinMode(pinI1,OUTPUT);
  pinMode(pinI2,OUTPUT);
  pinMode(speedpinA,OUTPUT);
  pinMode(pinI3,OUTPUT);
  pinMode(pinI4,OUTPUT);
  pinMode(speedpinB,OUTPUT);
   pinMode(pinI5,OUTPUT);
  pinMode(pinI6,OUTPUT);
  pinMode(speedpinC,OUTPUT);
  
  Serial.begin(9600);
  // We want to read the eeprom calibration...
}


void stop()//
{
    digitalWrite(speedpinA,LOW);// Unenble the pin, to stop the motor. this should be done to avid damaging the motor. 
     digitalWrite(speedpinB,LOW);
     digitalWrite(speedpinC,LOW);
}
// 1 means extend, -1 means restract
void activate_actuators(int actuator,int direction,int strength)
{
  analogWrite(act[actuator].speedPin,strength);
    if (direction == 1) {
      digitalWrite(act[actuator].reversePin,LOW);
      digitalWrite(act[actuator].forwardPin,HIGH);     
    } else if (direction == -1) {
      digitalWrite(act[actuator].reversePin,HIGH);
      digitalWrite(act[actuator].forwardPin,LOW);   
    }
}

void deactivate_actuator(int actuator) {
     digitalWrite(act[actuator].speedPin,LOW);
}

void output_sampled_array(int ms, int pin, int msPerOutput) {
  int tarray[ms];
  for (int i = 0; i < ms; i++ ) {
    tarray[i] = 0;
  }
 // read_for_time(ms, pin, tarray);
  long sum = 0;
  long cnt = 0;
  for (int i = 0; i < ms; i++) {
    sum += tarray[i];
    cnt++;
    if (cnt >= (ms / msPerOutput)) {
      if ((sum / cnt) > 0) {
        Serial.print(i);
        Serial.print(" ");
        Serial.println(sum / cnt);
      }
      sum = 0;
      cnt = 0;
    }
  }

}

// Note: if we used a transistor, we could turn off the LED when in
// Sleep mode.  This would be a significant benefit.
int readPositionVoltage() {
  int val = analogRead(ANALOG_VOLTAGE);
  Serial.println(val);
  return val;
}



void putCalibration() {
  for (int i = 0; i < 3; i++) {
    EEPROM.put(start_address + i * sizeof(actuator), act[i]);
  }
}
void getCalibration() {
  for (int i = 0; i < 3; i++) {
    EEPROM.get(start_address + i * sizeof(actuator), act[i]);
  }
}

void dumpCalibration() {
  for (int i = 0; i < 3; i++) {
    Serial.print(i);
    Serial.print(" ");
    Serial.println(act[i].minV);
    Serial.print(" + ");
    Serial.println(act[i].maxV);
  }
}

int sensePosition(int pin) {
  int val = analogRead(pin);
  return val;
}
// main_controller is my attempt to make a versitile
// reader from the serial port to control the
// variety of functions that we have.

void sensePositionVector(int v[]) {
  for(int i = 0; i < 3; i++) {
    v[i] = sensePosition(act[i].potPin);
  }
}
float dist(int a[],int b[]) {
  return sqrt((a[0] - b[0])*(a[0] - b[0]) + (a[1] - b[1])*(a[1] - b[1]) + (a[2] - b[2])*(a[2] - b[2]));
}
void OutputVector(int v[]) {
   for(int i = 0; i < 3; i++) {
     Serial.print(v[i]);
     Serial.print(" ");
   }
   Serial.println();
}

void move_vector(int *vec) {
  int cval[3];
  int dir[3];
 
 
  sensePositionVector(cval);
    const int tolerance = 50;
    const float STUCK_DISTANCE = 1.0; // millivolts  
  const int DELAY_TIME = 30;
  const int MAX_STUCK = 4;
    
    bool all_good = false;
  { // AAAA
   for(int i = 0; i < 3; i++) {
 //    dir[i] = sign(cval[i] - vec[i]);
    dir[i] = sign(vec[i] - cval[i]);
  }
  OutputVector(cval);
  Serial.println("Vector");
  OutputVector(dir);
  
  all_good = true;
     for(int i = 0; i < 3; i++) {
       if (abs(cval[i] - vec[i]) < tolerance) {
              deactivate_actuator(i);   
       } else {
           all_good = false;
       }
  }
 }


  int stuck_cnt = 0;

  while ((!all_good) && (stuck_cnt < MAX_STUCK)) {
    { // AAAA
     for(int i = 0; i < 3; i++) {
       // We can get stuck here and end up changing directions too often.  I need a better 
       // way of detecting that condition. We never really want to change directions more than once.
 //      dir[i] = sign(cval[i] - vec[i]);
     dir[i] = sign(vec[i] - cval[i]);      
       activate_actuators(i,dir[i],CRUISE_SPEED); 
     } 
     Serial.println("target:");
      OutputVector(vec);
       OutputVector(dir);
       OutputVector(cval);
     delay(DELAY_TIME); 
     int v[3];
     for(int i = 0; i < 3; i++) {
       v[i] = cval[i];     
     }
     
     sensePositionVector(cval);
     Serial.println(dist(v,cval));
     if (dist(v,cval) < STUCK_DISTANCE) {
       stuck_cnt++;
     } else {
       stuck_cnt = 0;
       Serial.println("ressetting stuck!");
     }
     
     
     OutputVector(cval);
     
     all_good = true;
     for(int i = 0; i < 3; i++) {
       if (abs(cval[i] - vec[i]) < tolerance) {
              deactivate_actuator(i);   
       } else {
           all_good = false;
       }
     }
    }
  }
  if (stuck_cnt >= MAX_STUCK) {
    Serial.println("GOT STUCK!");
  }

 for(int i = 0; i < 3; i++) {
    deactivate_actuator(i);
  }
  Serial.println("Move done!");
}

void test_via_extremes() {
  int v[3];
 for (int i = 0; i < 3; i++) {
   for (int j = 0; j < 3; j++) {
     for(int k = 0; k < 3; k++) {
       v[0] = i*500;
       v[1] = j*500;
       v[2] = k*500;
         move_vector(v);
         Serial.println("Made a move");
         OutputVector(v);
     }
   }
 }
}

// basic plan: Contract till you stop, record voltage
// then extend till you stop, record voltage!d
void calibrate(int actuator) {
 int val = sensePosition(act[actuator].potPin);
 const int DELAY_TIME = 5000;
 Serial.println(val);
 int cval = 1024;
 int dir = -1;
 while (val < cval) {
      activate_actuators(actuator,dir,255);
      delay(DELAY_TIME);
      deactivate_actuator(actuator);
      cval = val;
      val = sensePosition(act[actuator].potPin);
      Serial.println(val);
 } 
 act[actuator].minV = cval; 
  Serial.print("MinV = ");
 Serial.println(act[actuator].minV);
 
 dir = 1;
 cval = -1;
  while (val > cval) {
      activate_actuators(actuator,dir,255);
      delay(DELAY_TIME);
      deactivate_actuator(actuator);
      cval = val;
      val = sensePosition(act[actuator].potPin);
      Serial.println(val);
 } 
 act[actuator].maxV = cval; 
 

 Serial.print("MaxV = ");
 Serial.println(act[actuator].maxV);
 
}
// u0: actuator #0 open
// u1: actuator #0 stop
// u2: actuator #0 close
// v0: actuator #1 open
// v1: actuator #1 stop
// v2: actuator #1 close
void main_controller() {
  if (Serial.available()) {
    bool terminator_not_found = true;
    char inChar = Serial.read();
    Serial.println(inChar);
    // This stuff is for the MotorShield
    if (inChar == 'u' || inChar == 'v' || inChar == 'w') {
      int n = Serial.parseInt();
      int coil = (inChar == 'u') ? 0 : ((inChar == 'v') ? 1 : 2);
      if (n == 1) {
        deactivate_actuator(coil);
      } else {
      int dir = (n == 0) ? -1 : 1;
      Serial.println("Direction:");
      if (dir == 1) Serial.println("extend");
      if (dir == -1) Serial.println("retract");
      activate_actuators(coil,dir,255);
      }
    }
    
    if (inChar == 't') {
      for(int i = 0; i < 1; i++) {
       test_via_extremes();
      }
    }
    
    if (inChar == 'd') {
      dumpCalibration();
    }
    if (inChar == 'c') {
      int n = Serial.parseInt();
      if (n < 0 || n > 2) {
        Serial.println("bad actuator");
      } 
      calibrate(n);
    }
    if (inChar == 'r') {
      int n = Serial.parseInt();
      if (n < 0 || n > 2) {
        Serial.println("bad actuator");
      } 
      int val = sensePosition(act[n].potPin);
      Serial.print("value of ");
      Serial.print(act[n].potPin);
      Serial.print(" = ");
      Serial.println(val);
    }
    
      if (inChar == 'a') {
      char comma = Serial.read();
      int vec[3];
      vec[0] = Serial.parseInt();
      comma = Serial.read();
      vec[1] = Serial.parseInt();
      comma = Serial.read();
      vec[2] = Serial.parseInt();
      Serial.println("XXX");
      OutputVector(vec);
      move_vector(vec);
      OutputVector(vec);
    }
 
    if (inChar == 'z') {
      dumpCalibration();
      putCalibration();
    }
    if (inChar == 'g') {
      getCalibration();
      dumpCalibration();
    }
    if (inChar == '\n') {
      terminator_not_found = false;
    }
    if (terminator_not_found) {
    while (!Serial.available()) ;
    char terminator = Serial.read();
    if (terminator != '\n') {
      Serial.print(terminator);
      Serial.println(" : Didn't read terminator successfully.");
    }
    }
  }
}


void loop() {
  main_controller();

}

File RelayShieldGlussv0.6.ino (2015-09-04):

#include <stdlib.h>
#include <EEPROM.h>
#include <assert.h>

int Ppos = 7;
int Pneg = 6;
int Qpos = 5;
int Qneg = 4;

int ANALOG_PIN_P = 0;
int ANALOG_PIN_Q = 1;
int ANALOG_PIN_POT = 5;
const int ANALOG_VOLTAGE = 3;

// Calibratio[x] is meant to be the voltage read from our position sensor
// and position x.  At present, there is some confustion about what the
// Position "p" really means. My goal is to standardize "p == 0" to mean
// "Fully retracted".  I actually need to clean up the language of much of this file.

const int NUM_POSITIONS = 14; // This will be rougly the 2 x the number of magnets in the current approach.
int Calibration[14];


// In fact Speed is not used with relays
int FULLSPEED = 255;



// This a relative position.  I am attempting
// to move toward an absolute position.
// This is the model of our actuator.
// P is the position of the P coil in 1/2" increments.
int p = 0;
// Q is the position of the Q coil in 1/2" increments.
// By structure, Q = P + 3
int q() {
  return p + 3;
}

// apos represents our current understanding of our digital 
// position (measured in 1/2" intervals, with 0 being full retraction.
int apos = 0;

int compute_p_from(int apos) {
  int px;
  px = apos % 4;
//  px = px + 0;
//  px = px + 1;
//  px = px + 2;
//  px = px + 3;
  return px; 
}

void set_calibration_to_hand_code() {
  Calibration[0] = 325;
  Calibration[1] = 365;
  Calibration[2] = 401;
  Calibration[3] = 438;
  Calibration[4] = 471;
  Calibration[5] = 506;
  Calibration[6] = 528;
  Calibration[7] = 552;
  Calibration[8] = 573;
  Calibration[9] = 594;
  Calibration[10] = 613;
  Calibration[11] = 633;
  Calibration[12] = 649;
  Calibration[13] = 665;
}
// Here we update our two model variables by reading our sensor position...
void update_model() {
   int val = sensePosition();
   int dpos = digitizePosition(val);
   apos = dpos;
   p = compute_p_from(apos);
}

// The polarity of any position is given by this funciton...
// +1 means North to the right, -1 means South to the right (postive x), 0 means unstable.
// Someday this could be a continuous function....if we every try to get continuos
// resolutin from our 2-coil system.
// The period of polarity is 4 (in half inches).
int polarity(int pos) {
  while (pos < 0) pos += 1000;
  int modpos = pos % 4;
  //  Serial.print("Position:");
  //  Serial.println(pos);
  //  Serial.println("Modpos:");
  //  Serial.println(modpos);
  switch (modpos) {
    case 0:
      return 0;
    case 1:
      return 1;
    case 2:
      return 0;
    case 3:
      return -1;
  }

}


void setup()
{
  pinMode(Ppos, OUTPUT);
  pinMode(Pneg, OUTPUT);
  pinMode(Qpos, OUTPUT);
  pinMode(Qneg, OUTPUT);
  pinMode(ANALOG_PIN_P, INPUT);
  pinMode(ANALOG_PIN_Q, INPUT);
  pinMode(ANALOG_VOLTAGE, INPUT);
  Serial.begin(38400);
  // We want to read the eeprom calibration...
  getCalibration();
  dumpCalibration();
}


void stop()//
{

}

void activate(int coil, int direction, int strength) {
  if (coil == 0) {
    if (direction == 1) {
      // Just to be sure we will make sure other is turned off!
      digitalWrite(Pneg, LOW);
      delay(10);
      digitalWrite(Ppos, HIGH);
    } else if (direction == -1) {
      // Just to be sure we will make sure other is turned off!
      digitalWrite(Ppos, LOW);
      delay(10);
      digitalWrite(Pneg, HIGH);
    }
  } else if (coil == 1) {
    if (direction == 1) {
      // Just to be sure we will make sure other is turned off!
      digitalWrite(Qneg, LOW);
      delay(10);
      digitalWrite(Qpos, HIGH);
    } else if (direction == -1) {
      // Just to be sure we will make sure other is turned off!
      digitalWrite(Qpos, LOW);
      delay(10);
      digitalWrite(Qneg, HIGH);
    }
  }
}
void deactivate(int coil) {
  if (coil == 0) {
    digitalWrite(Ppos, LOW);
    digitalWrite(Pneg, LOW);
  } else {
    digitalWrite(Qpos, LOW);
    digitalWrite(Qneg, LOW);
  }

}
// This is an experimental attempt to move fast and smoothly
// by modifying activation time.
const float TIME_MULTIPLE = 2.0;
void moveHalfInches(int n, int s) {
  if (n == 0) return;
  int kickstart_time = 200 * TIME_MULTIPLE;
  int duration_time = 200 * TIME_MULTIPLE;
  int end_time = 200 * TIME_MULTIPLE;
  //  int kickstart_time = 5000;
  //  int duration_time = 500;
  //  int end_time = 500;
  if (n > 0) {
    moveHalfInch(s, kickstart_time);
  }
  for (int i = 1; i < n - 1; i++) {
    moveHalfInch(s, duration_time);
  }
  if (n > 1) {
    for (int i = n - 1; i < n; i++) {
      moveHalfInch(s, end_time);
    }
  }
  int val = analogRead(ANALOG_VOLTAGE);
  Serial.print("VOLTAGE = ");
  Serial.println(val);
}

// Now, to move half an inch, we have
// to deside which coil has polarity.
// We then push that coil according to the polarity, and
// update the position.
// Positive means move right, negative means move left.
void moveHalfInch(int s, int activation_time) {
  moveHalfInchOpenLoop(s, activation_time);
  //  moveHalfInchClosedLoop(s,activation_time);
  return;
}
void moveHalfInchOpenLoop(int s, int activation_time) {
  // 0 means the P Coil, 1 means the Q Coil.
  int coilWithPolarity = (polarity(p) == 0) ? 1 : 0;
  int polarityOfCoil = (coilWithPolarity) ? polarity(q()) : polarity(p);

  Serial.print("p = ");
  Serial.print(p);
  Serial.print(" C: ");
  Serial.print(coilWithPolarity);
  Serial.print(" s:");
  Serial.println(s * polarityOfCoil);
  activate(coilWithPolarity, s * polarityOfCoil, FULLSPEED);
  delay(activation_time);
  deactivate(coilWithPolarity);

  // Now make the model reflect the update
//  p += s;
  update_model();
}




int playCnt = 0;

const int ACTIVATION_TIME = 500;


void experiment2() {
  for (int i = 0; i < 6; i++ ) {

    moveHalfInches(4 + i, 1);
    delay(100);
    moveHalfInches(4 + i, -1);
    delay(100);
  }
}

void experiment3() {
  if (Serial.available()) {
    char inChar = Serial.read();
    Serial.println(inChar);
    while (!Serial.available() > 0) ;
    if (inChar == 'l' || inChar == 'r') {
      int n = Serial.parseInt();
      Serial.println(n);
      Serial.println("About to call!");
      Serial.println((inChar == 'l') ? -1 : 1);
      moveHalfInches(n, (inChar == 'l') ? -1 : 1);
      //     holdPosition(500);
    }
    while (Serial.read() == '\n') ;
  }
}

// void moveToPosition(int newp) {
//  int d = newp - p;
//  Serial.print("About to call moveHalfInches");
//  Serial.println((int)d);
//  moveHalfInches((int)abs(d), (d < 0) ? -1 : 1);
// }
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

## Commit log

2015-08-29 Adding phsycial models, though better shard through Fusion 360
    [StatorEndCap.stl, StatorForStandardSize.stl, StatorForStandardV7.stl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]
2015-09-04 Latest version of relay shield code, working with sensor to provide absolute positioning (Calibration must be done by hand due to stickiness.)
2015-09-26 adding stls
    [EndCapForStator12mm.stl, StatorEndCap.stl, StatorForStandardV7.stl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]
2015-10-27 adding latest Arduino code
